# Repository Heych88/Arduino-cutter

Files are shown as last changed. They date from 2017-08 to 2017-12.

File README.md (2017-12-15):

# Arduino-cutter
Arduino controller implementation of a plastic or resistor cutter.

The controller daughter board contains the follow external board connections;

 * 6 -> 14v
 * Four push-buttons
 * Adjustable potentiometer
 * E-stops
 * 4-bit LCD
 * Single pulse encoder
 * Two solenoid relays, active low, 5v or Vin
 * Stepper motor, 2A
 * Fuse connector

## Hardware Setup

The parts required and the daughterboard PCB Gerber files are located in the EagleBoard folder.

The interfacing of the components is as follows.

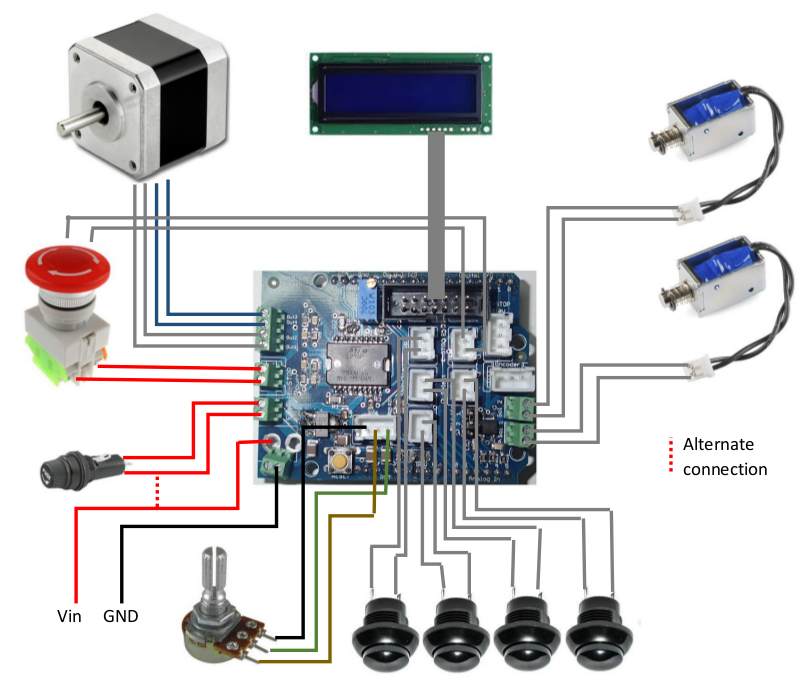
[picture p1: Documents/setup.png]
system interfacing


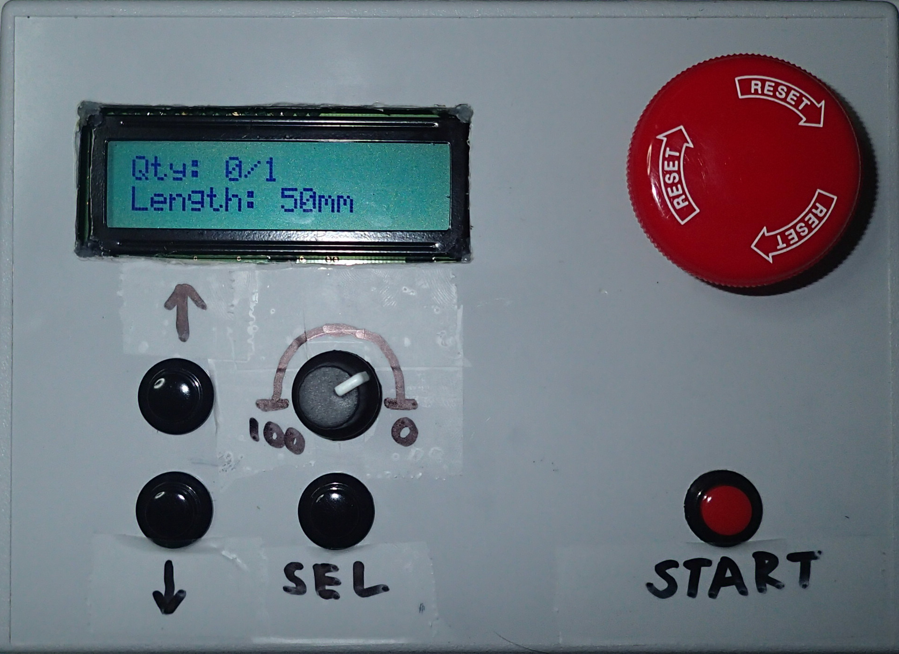
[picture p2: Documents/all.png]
assembled box


## Installing

1. Clone this repository

 ```sh
 git clone https://github.com/Heych88/Arduino-cutter.git
 ```

2. Download Arduino IDE from [here](https://www.arduino.cc/en/Main/Software).

3. If you are installing a brand-new Arduino Leonardo board, the EEPROM must be flashed first. If it is the existing system board, continue from step 4.

 1. Load the `eeprom_write.ino` file, located in the `/src/eeprom_write/` folders, into the Arduino IDE.

 2. Compile and load the file onto the Arduino board.

4. Load any of the `.ino` files, located in the `/src/` folders, into the Arduino IDE.

5. Compile and load the files onto the Arduino board.

Detailed programming and system information can be found in the *Arduino Cutter Instructions* document, located in the `/documents/` folder.

## Usage

This repository provides a daughterboard and usable code to run an Arduino plastic or resistor cutter.

## Contributing

1. Fork it!
2. Create your feature branch: `git checkout -b my-new-feature`
3. Commit your changes: `git commit -am 'Add some feature'`
4. Push to the branch: `git push origin my-new-feature`
5. Submit a pull request :D

## License

This project is licensed under the GNU-GPL3 License - see the [LICENSE.md](LICENSE.md) file for details.

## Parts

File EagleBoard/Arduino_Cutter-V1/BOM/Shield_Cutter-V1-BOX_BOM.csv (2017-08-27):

Qty | Value | MPN | Digi-key | Description
1 |  | QPC02SXGN-RC | S9337-ND | CONN JUMPER SHORTING .100" GOLD
1 |  | 61300311121 | 732-5316-ND | 3 Positions Header Connector 0.100" (2.54mm) Through Hole
1 |  | 2047 | 1528-2164-ND | POTENTIOMETER KNOB - SOFT TOUCH
1 |  | P160KN-0QC15B100K | 987-1300-ND | 100k Ohm Gang Linear Panel Mount Potentiometer None 1 Turn Conductive Plastic 0.2W, 1/5W PC Pins
1 |  | NHD-0216K1Z-FSB-GBW-L | NHD-0216K1Z-FSB-GBW-L-ND | Character LCD Display Module Transflective 5 x 8 Dots STN - Super-Twisted Nematic LED - Blue Parallel 80.00mm x 36.00mm x 13.50mm
1 |  | ROB-09238 | 1568-1105-ND | Bipolar Stepper Motor 200 Step 0.33A 12VDC
1 |  | 101-146 | ED10501-ND | 14 Position Rectangular Socket Connector IDC
1 |  | A165E-S-02 | Z1428-ND | Pushbutton Switch DPST-NC Emergency Stop Panel Mount
6 |  | XHP-2 | 455-2266-ND | 2 Position Rectangular Housing Connector Receptacle Natural 0.098" (2.50mm)
3 |  | XHP-3 | 455-2219-ND | 3 Position Rectangular Housing Connector Receptacle Natural 0.098" (2.50mm)
18 |  | SXH-001T-P0.6 | 455-1135-1-ND | Contact Crimp Socket 22-28 AWG Tin
1 |  | 1-640454-6 | A106877-ND | 16 Positions Header Connector 0.100" (2.54mm) Through Hole Tin
1 |  | 4-643814-6 | A30966-ND | 16 Position Rectangular Receptacle Connector IDC Tin 24 AWG
3 |  | RP3502ABLK | EG1900-ND | Pushbutton Switch SPST-NO Standard Panel Mount, Front, Black
1 |  | RP3502ARED | EG1930-ND | Pushbutton Switch SPST-NO Standard Panel Mount, Front, Red
1 |  | 17S,GY | SR17SG-ND | Box Plastic, ABS Gray Split Sides and Slanted Top 6.880" L x 4.880" W (174.75mm x 123.95mm) X 2.490" (63.25mm)
1 |  | A000057 | 1050-1040-ND | ATmega32U4 Arduino Leonardo AVR® ATmega MCU 8-Bit AVR Embedded Evaluation Board

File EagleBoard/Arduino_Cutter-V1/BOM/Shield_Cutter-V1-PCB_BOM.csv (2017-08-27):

Qty | Value | MPN | Digi-key | Package | Parts | Description
1 |  | 61300311121 | 732-5316-ND | JP2 | JP1 | CONN HEADER 3 POS 2.54
2 | 0R15 | RL1206FR-7W0R15L | 311-.15LYCT-ND | R1206 | R1, R2 | RES SMD 0.15 OHM 1% 1/2W 1206
1 |  | B3F-1002 | SW401-ND | B3F-10XX | RESET | SWITCH TACTILE SPST-NO 0.05A 24V
6 | 100nF | C0805C104K5RACTU | 399-1170-1-ND | C0805 | C3, C6, C7, C8, C9, C10 | 0.1µF ±10% 50V Ceramic Capacitor X7R 0805 (2012 Metric)
1 | 10k | PV36W103C01B00 | 490-2875-ND | S64W | R29 | POTENTIOMETER
12 | 10kΩ | RMCF0805FT10K0 | RMCF0805FT10K0CT-ND | R0805 | R3, R4, R10, R12, R17, R18, R19, R20, R22, R23, R25, R27 | ±1% 0.125W, 1/8W Chip Resistor 0805 (2012 Metric)
4 | 10u 35V | C1210C106K3RACTU | 399-8224-1-ND | C1210 | C1, C2, C4, C5 | CAPACITOR, European symbol
6 | 10Ω | RC0805FR-0710RL | RMCF0805FT10R0CT-ND | R0805 | R9, R11, R21, R24, R26, R28 | RES SMD 10 OHM 1% 1/8W 0805
4 | 1kΩ | RMCF0805FT1K00 | RMCF0805FT1K00CT-ND | R0805 | R5, R6, R7, R8 | ±1% 0.125W, 1/8W Chip Resistor 0805 (2012 Metric)
3 | 22-23-2021 | OSTVN02A150 | ED10561-ND | 22-23-2021 | X1, X4, X5 | .100" (2.54mm) Center Header - 2 Pin
1 | 22-23-2041 | OSTVN04A150 | ED10563-ND | 22-23-2041 | X2 | CONN TERM BLOCK 2.54MM 4POS PCB
1 | 2514- | 302-S141 | ED10522-ND | PAK100/2500-14 | X5 | 14 Positions Header Connector 0.100" (2.54mm) Through Hole
4 | 330Ω | RMCF0805FT330R | RMCF0805FT330RCT-ND | R0805 | R13, R14, R15, R16 | ±1% 0.125W, 1/8W Chip Resistor 0805 (2012 Metric)
2 | 40v | BAT54AW,115 | 1727-3567-1-ND | SOT323 | D10, D11 | Diode Array 1 Pair Common Anode Schottky 200mA (DC) Surface Mount SC-70, SOT-323
2 | AQY21SOP | CPC1020NTR | CLA318CT-ND | SOP04 | K1, K2 | PhotoMOS Relay NAiS
6 | Green | LG R971-KN-1 | 475-1410-1-ND | CHIPLED_0805 | L1, L2, L3, L4, L5, L6 | LED GREEN DIFFUSED 0805 SMD
1 | L298P | L298P | 497-1396-5-ND | POWER-SO20 | IC1 | L298P DUAL FUL-BRIDGE DRIVER PowerSO20
1 | REG1117 | REG1117-5/2K5 | 296-27924-1-ND | SOT223 | IC2 | 800mA and 1A Low Dropout (LDO) Positive Regulator
6 | S2B-PH-K | B2B-XH-A(LF)(SN) | 455-2247-ND | S02P | SV1, SV3, SV4, SV5, SV6, SV7 | CONN HEADER XH TOP 2POS 2.5MM
3 | S3B-PH-K | B3B-XH-A(LF)(SN) | 455-2248-ND | S03P | SV2, SV8, SV9 | CONN HEADER XH TOP 3POS 2.5MM
9 | SS14 | MBRAF360T3G | MBRAF360T3GOSCT-ND | SMA | D1, D2, D3, D4, D5, D6, D7, D8, D9 | DIODE SCHOTTKY 60V 4A SMA

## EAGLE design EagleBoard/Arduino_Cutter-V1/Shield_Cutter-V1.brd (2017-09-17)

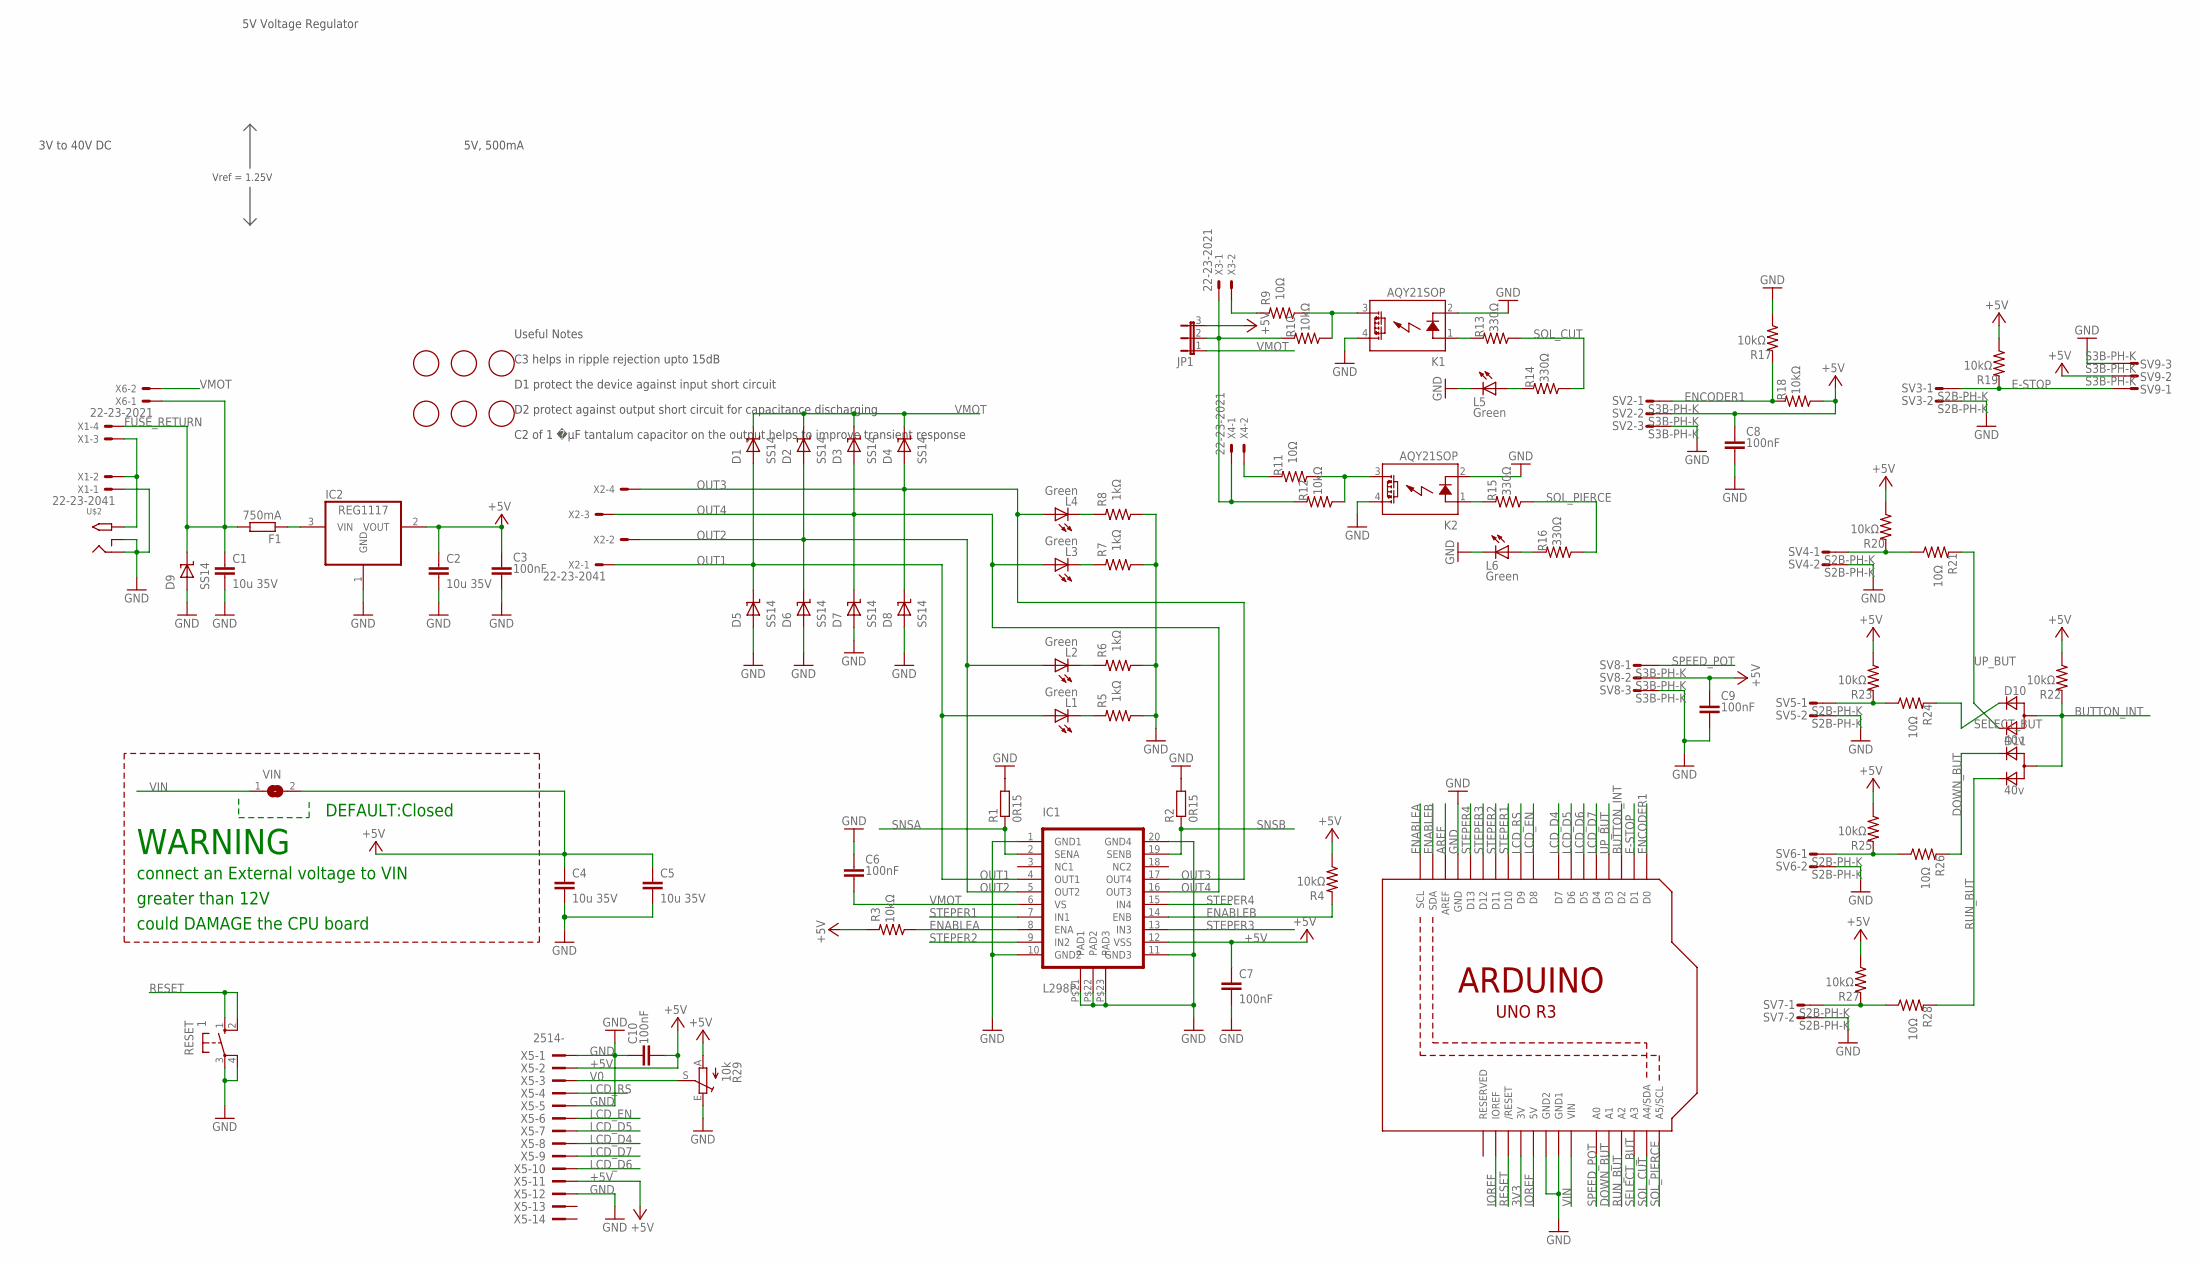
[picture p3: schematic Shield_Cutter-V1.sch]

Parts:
C1, C2, C4, C5: 10u 35V; C1210
C3, C6, C7, C8, C9, C10: 100nF; C0805
D1, D2, D3, D4, D5, D6, D7, D8, D9: SS14; SMA
D10, D11: 40v; SOT323
F1: 750mA; R1206
FID1, FID2, FID3, FID4, FID5, FID6: FIDUCIALMOUNT; FIDUCIA-MOUNT
IC1: L298P; POWER-SO20
IC2: REG1117; SOT223
JP1: JP2E; JP2
K1, K2: AQY21SOP; SOP04
L1, L2, L3, L4, L5, L6: Green; CHIPLED_0805
R1, R2: 0R15; R1206
R3, R4, R10, R12, R17, R18, R19, R20, R23, R25, R27: 10kΩ; R0805
R5, R6, R7, R8: 1kΩ; R0805
R9, R11, R21, R24, R26, R28: 10Ω; R0805
R13, R14, R15, R16: 330Ω; R0805
R22: 10kΩ; M0805
R29: 10k; S64W
RESET: 1; B3F-10XX
SV2, SV8, SV9: S3B-PH-K; S03P
SV3, SV4, SV5, SV6, SV7: S2B-PH-K; S02P
U1: ARDUINOR3-DIMENSION; ARDUINOR3
U$2: 2.1MMJACKTHM; PJ-102A
VIN: SJW
X1, X2: 22-23-2041
X3, X4, X6: 22-23-2021
X5: 2514-; PAK100/2500-14

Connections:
3V3: U1.3V
+5V: C2.1, C3.1, C4.1, C5.1, C7.1, C8.1, C9.1, C10.2, IC1.P$12 (VSS), IC2.2 (VOUT), JP1.3, R3.2, R4.1, R18.1, R19.1, R20.1, R22.1, R23.1, R25.1, R27.1, R29.A, SV2.2, SV8.2, SV9.2, VIN.2, X5.2, X5.11
AREF: U1.AREF
BUTTON_INT: D10.1 (A), D11.1 (A), R22.2, U1.D2
DOWN_BUT: D11.2 (C1), R26.2, U1.A1
E-STOP: R19.2, SV3.1, SV9.1, U1.D1
ENABLEA: IC1.P$8 (ENA), R3.1, U1.SCL
ENABLEB: IC1.P$14 (ENB), R4.2, U1.SDA
ENCODER1: R17.2, R18.2, SV2.1, U1.D0
FUSE_RETURN: C1.1, D9.P$1 (K), F1.2, X1.4, X6.1
GND: C1.2, C2.2, C3.2, C4.2, C5.2, C6.1, C7.2, C8.2, C9.2, C10.1, D5.P$2 (A), D6.P$2 (A), D7.P$2 (A), D8.P$2 (A), D9.P$2 (A), IC1.P$1 (GND1), IC1.P$10 (GND2), IC1.P$11 (GND3), IC1.P$20 (GND4), IC1.P$21 (PAD1), IC1.P$22 (PAD2), IC1.P$23 (PAD3), IC2.1 (GND), K1.2 (K), K1.4 (DS1), K2.2 (K), K2.4 (DS1), L5.C, L6.C, R1.2, R2.2, R5.1, R6.1, R7.1, R8.1, R17.1, R29.E, RESET.3, RESET.4 (P1), SV2.3, SV3.2, SV4.2, SV5.2, SV6.2, SV7.2, SV8.3, SV9.3, U1.GND, U1.GND1, U1.GND2, U$2.RING, U$2.RING_SW, X1.1, X5.1, X5.5, X5.12
IOREF: U1.5V, U1.IOREF
LCD_D4: U1.D7, X5.8
LCD_D5: U1.D6, X5.7
LCD_D6: U1.D5, X5.10
LCD_D7: U1.D4, X5.9
LCD_EN: U1.D8, X5.6
LCD_RS: U1.D9, X5.4
unnamed: L4.C, R8.2
unnamed: L3.C, R7.2
unnamed: L2.C, R6.2
unnamed: L1.C, R5.2
unnamed: K1.1 (A), R13.2
unnamed: L5.A, R14.2
unnamed: R9.2, X3.2
unnamed: R23.2, R24.1, SV5.1
unnamed: JP1.2, R10.2, R12.2, X3.1, X4.1
unnamed: K2.3 (DS2), R11.1, R12.1
unnamed: L6.A, R16.2
unnamed: R20.2, R21.1, SV4.1
unnamed: K2.1 (A), R15.2
unnamed: R11.2, X4.2
unnamed: K1.3 (DS2), R9.1, R10.1
unnamed: R25.2, R26.1, SV6.1
unnamed: F1.1, IC2.3 (VIN)
unnamed: R27.2, R28.1, SV7.1
OUT1: D1.P$2 (A), D5.P$1 (K), IC1.P$4 (OUT1), L1.A, X2.1
OUT2: D2.P$2 (A), D6.P$1 (K), IC1.P$5 (OUT2), L2.A, X2.2
OUT3: D4.P$2 (A), D8.P$1 (K), IC1.P$17 (OUT4), L4.A, X2.4
OUT4: D3.P$2 (A), D7.P$1 (K), IC1.P$16 (OUT3), L3.A, X2.3
POWERIN: U$2.TIP, X1.2, X1.3
RESET: RESET.1 (S), RESET.2 (S1), U1.RESET (/RESET)
RUN_BUT: D11.3 (C2), R28.2, U1.A2
SELECT_BUT: D10.2 (C1), R24.2, U1.A3
SNSA: IC1.P$2 (SENA), R1.1
SNSB: IC1.P$19 (SENB), R2.1
SOL_CUT: R13.1, R14.1, U1.A4 (A4/SDA)
SOL_PIERCE: R15.1, R16.1, U1.A5 (A5/SCL)
SPEED_POT: SV8.1, U1.A0
STEPER1: IC1.P$7 (IN1), U1.D10
STEPER2: IC1.P$9 (IN2), U1.D11
STEPER3: IC1.P$13 (IN3), U1.D12
STEPER4: IC1.P$15 (IN4), U1.D13
UP_BUT: D10.3 (C2), R21.2, U1.D3
V0: R29.S, X5.3
VIN: U1.VIN, VIN.1
VMOT: C6.2, D1.P$1 (K), D2.P$1 (K), D3.P$1 (K), D4.P$1 (K), IC1.P$6 (VS), JP1.1, X6.2

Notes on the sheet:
WARNING
connect an External voltage to VIN
greater than 12V
could DAMAGE the CPU board
DEFAULT:Closed
5V Voltage Regulator
C3 helps in ripple rejection upto 15dB
D1 protect the device against input short circuit
D2 protect against output short circuit for capacitance discharging
C2 of 1 �µF tantalum capacitor on the output helps to improve transient response
Useful Notes
5V, 500mA
3V to 40V DC
Vref = 1.25V

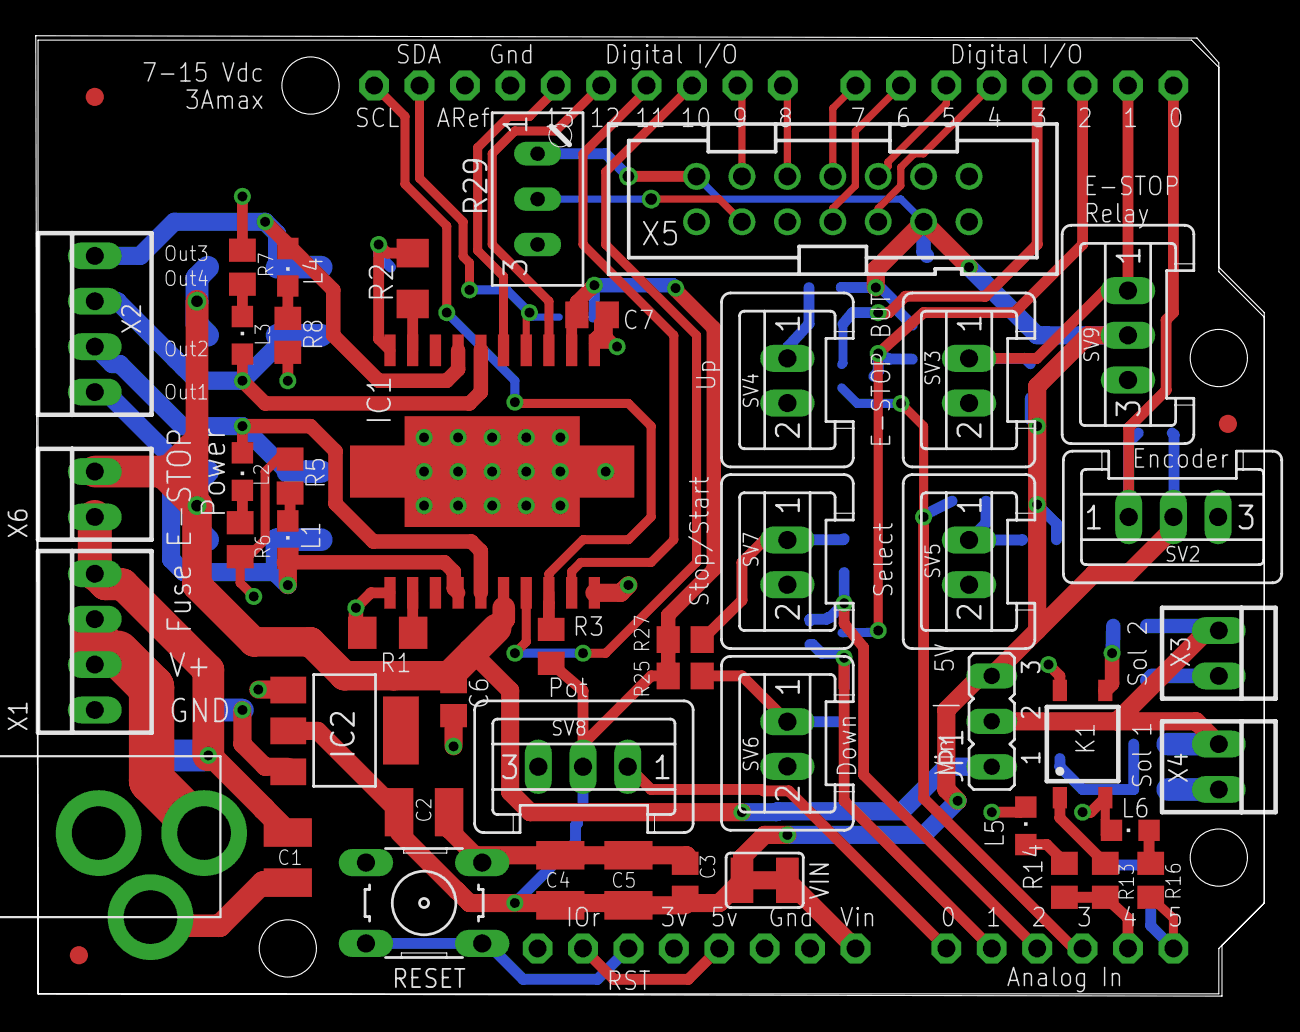
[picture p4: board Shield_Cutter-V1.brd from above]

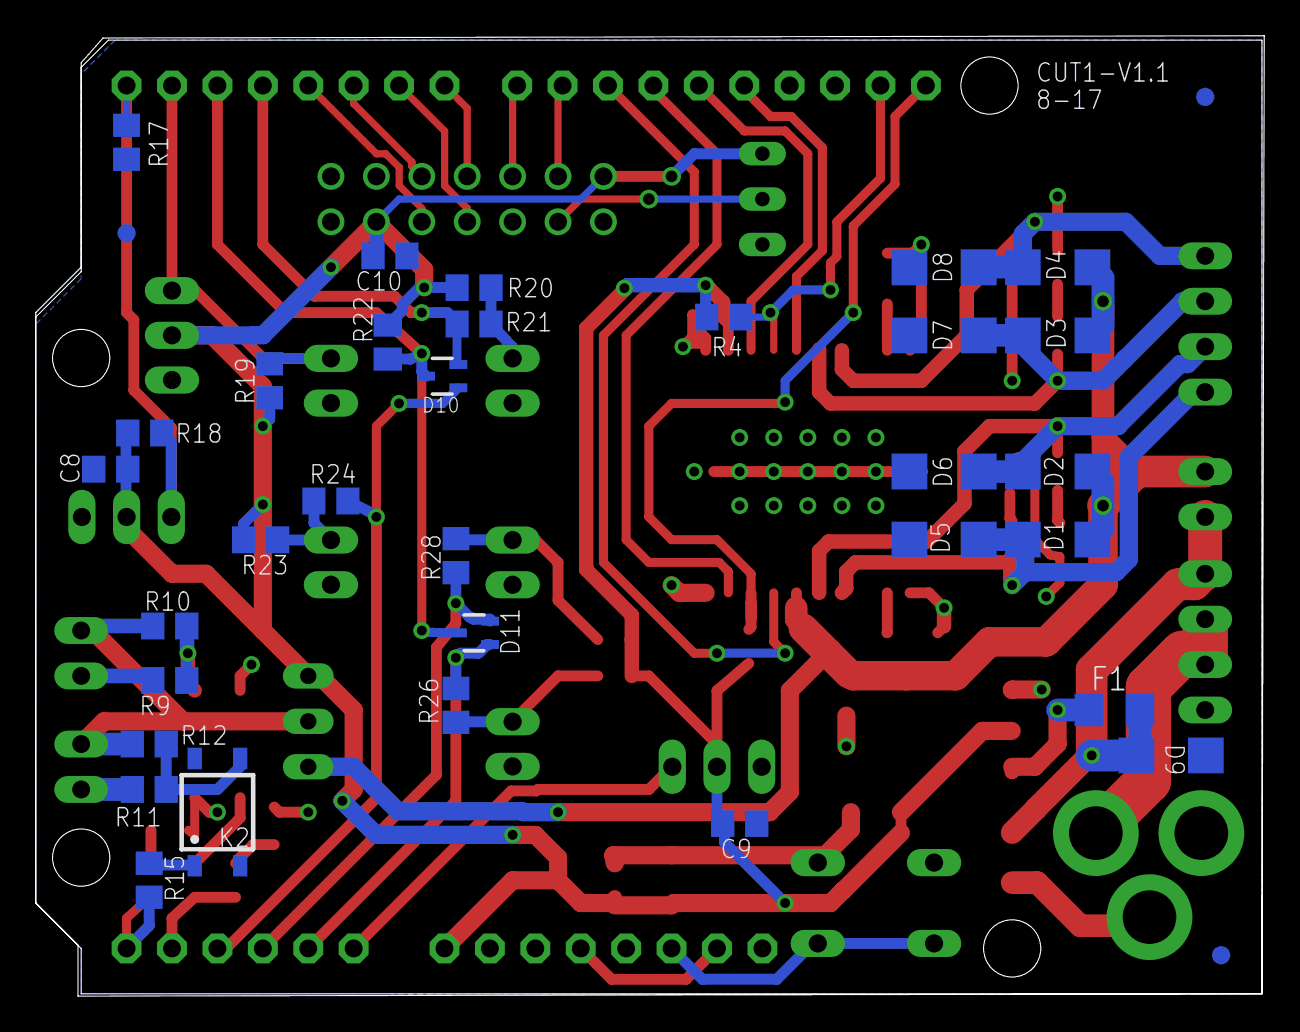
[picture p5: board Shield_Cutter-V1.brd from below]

Board: 2 copper layers, 68.7 x 53.7 mm, 86 parts (35 on the bottom side), 55 nets.

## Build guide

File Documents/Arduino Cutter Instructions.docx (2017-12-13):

# Setup

## Specifications

Power supply: 6 -> 14vdc, center positive

Fuse: 3A Max, 5x20mm glass fuse

Solenoid: 5v or Vin

Stepper motor: Vin, 5mm shaft, bipolar

## Hardware Setup

The system contains the follow external board connections;

- Five push-buttons
- Adjustable potentiometer
- Two E-stops, one active, one passive.
- 4-bit LCD
- Single pulse encoder
- Two solenoid relays, active low
- Stepper motor driver
- Fuse connector
- Power

The hardware parts list, PCB files and program, can be downloaded from the Git repository;

https://github.com/Heych88/Arduino-cutter

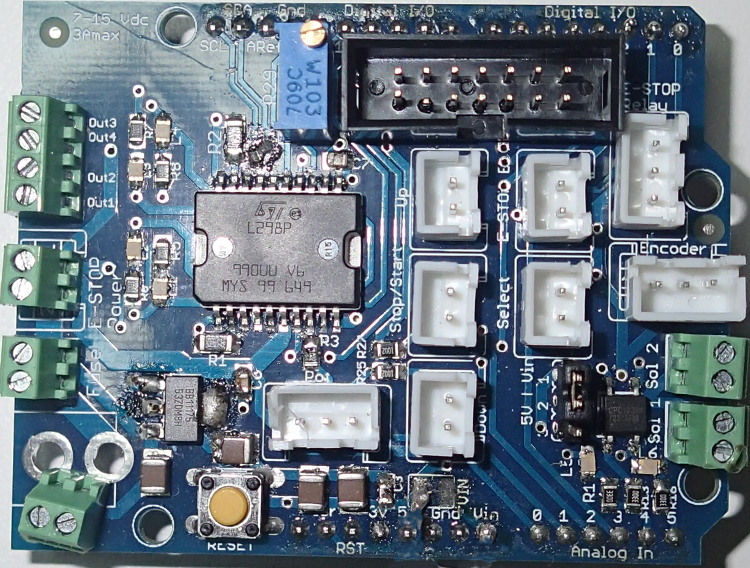
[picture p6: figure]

Stepper motor

E-stop return

E-stop Vin

Fuse return

Fuse Vin

Vin

Solenoid outputs

4-bit LCD

Solenoid voltage select

GND

Reset

E-stop sense

Up PB

E-stop active S + -

S

Select PB

Stop/Start PB

S

S

Encoder S + -

Pot - + S

Down PB

The wiring of the hardware, for most common operations, is as follows;

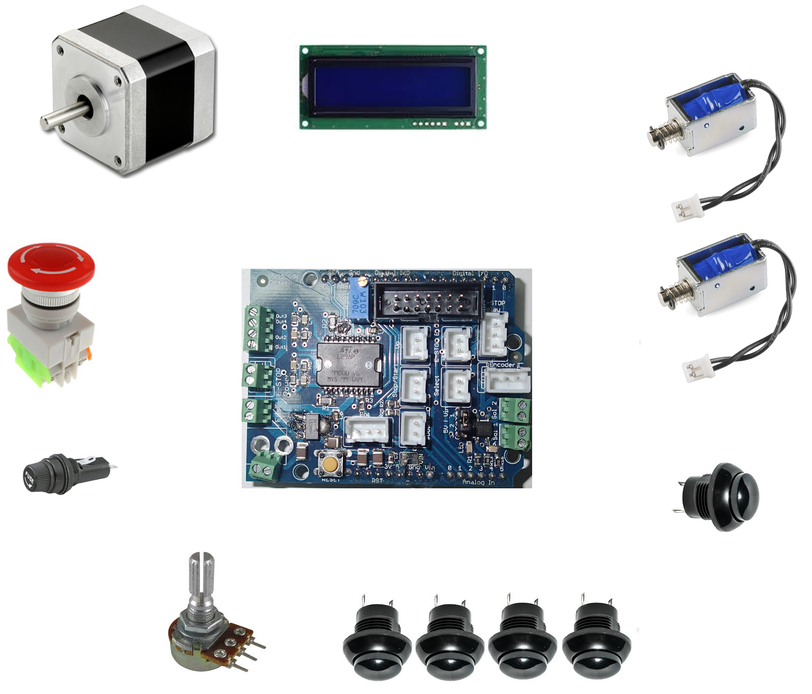
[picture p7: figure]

Alternate connection

Pierce

Cut

Up Down Stop/Stat Select

Vin GND

### Motor rotation direction

Upon installation of a stepper motor, the two winding pairs must be located. It is recommended to use a multimeter to measure the resistance between the wires. One winding pair must then be connected into the output connector group pairing of Out1 and Out2 and the second winding pair connected to Out3 and Out4.

Once connected, the motor will spin in a direction. If the motor is required to spin in the reverse direction, swap the group pairings with each other. I.e. Out1 swap with Out3, Out2 swap with Out4.

### Solenoid power selection

The solenoids can be supplied with either 5v or Vin. Both solenoids must power from the same supply and must both be either 5v or Vin.

The voltage can be changed by swapping the jumper on header JP1. See board for voltage configuration details.

For 5v solenoids, place the jumper on pins 1 and 2. For Vin solenoids, put the jumper on pins 2 and 3.

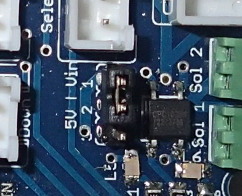
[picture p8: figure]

## Software Setup

### Menu Selection

The controller contains 11 adjustable menu selections. Six for adjusting production runs and five for system specific hardware setup.

To enter the system menu, press the up button.

To navigate the system menu, press either the up or down buttons.

To select a menu, press the SEL button, and a flashing cursor will appear on the screen.

### Production Run Settings

#### Adjust quantity

Adjusts the desired production quantity to be produced with the desired product specifications, as outlined in other sections.

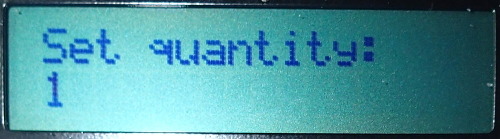
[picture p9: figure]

1. Navigate to the "Set quantity" menu using the UP or DOWN buttons.
2. Press the SEL button, and a flashing cursor will appear. If the flashing cursor doesn’t appear, press the SEL button until it does.
3. Adjust the desired quantity using the UP or DOWN buttons.
4. Press the SEL button to set the desired quantity and return to the home screen.

#### Adjust length

Adjusts the total desired product length.

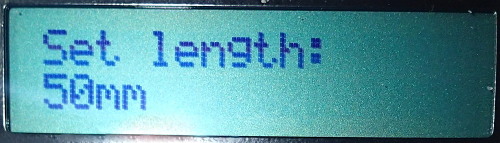
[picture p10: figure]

1. Navigate to the "Set length" menu using the UP or DOWN buttons.
2. Press the SEL button, and a flashing cursor will appear. If the flashing cursor doesn’t appear, press the SEL button until it does.
3. Adjust the desired length using the UP or DOWN buttons.
4. Press the SEL button to set the desired length and return to the home screen.

#### Reset production counts

Resets the number of the already produced product.

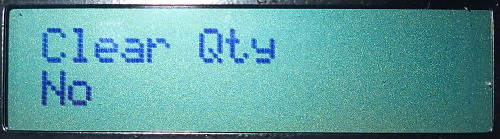
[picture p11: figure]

1. Navigate to the "Clear Qty" menu using the UP or DOWN buttons.
2. Press the SEL button, and a flashing cursor will appear. If the flashing cursor doesn’t appear, press the SEL button until it does.
3. Press the UP button until the display changes to "Yes".
4. Press the SEL button to rest the produced quantity and return to the home screen.

#### Adjust motor speed menu

Adjusts the motors running speed. This menu is only used for display purposes only.

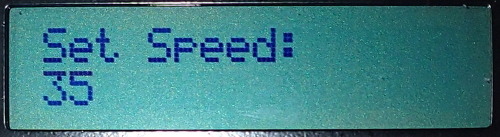
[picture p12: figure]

1. Navigate to the "Set Speed" menu using the UP or DOWN buttons.
2. Adjust the speed using the SPEED DIAL until at the desired speed.
3. Navigate to the home menu with the DOWN button.

#### Adjust pierce distance

Adjusts the distance from the end of the desired length to add a pierce.

If the number of pierces is two, a pierce is performed at the desired distance from the start of piece and the desired distance from the final length of the part.

If the number of pierces is one, a pierce is only performed at the desired distance from the start of piece.

The pierce distance is calculated from the product edges and the centre of the piercing die.

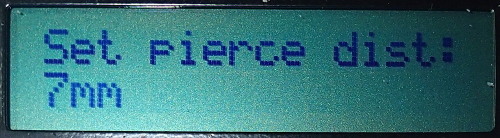
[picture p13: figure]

1. Navigate to the "Set pierce dist" menu using the UP or DOWN buttons.
2. Press the SEL button, and a flashing cursor will appear. If the flashing cursor doesn’t appear, press the SEL button until it does.
3. Adjust the desired length using the UP or DOWN buttons.
4. Press the SEL button to set the desired distance and return to the home screen.

#### Adjust pierce quantity

Resets the number of piercings in each product piece.

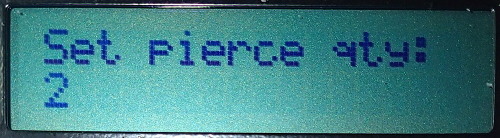
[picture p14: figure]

1. Navigate to the "Set pierce qty" menu using the UP or DOWN buttons.
2. Press the SEL button, and a flashing cursor will appear. If the flashing cursor doesn’t appear, press the SEL button until it does.
3. Adjust the desired quantity using the UP or DOWN buttons.
4. Press the SEL button to set the quantity and return to the home screen.

### Hardware Setup

#### Adjust pierce solenoid delay

Adjusts the time delay for activating and deactivating the solenoid used for piercing in milliseconds.

The total solenoid time is double the delay time set, as the delay time set is the full time that the solenoid is activated (set Low) and the identical time to release and retract the solenoid (set High) back to its deactivated state.

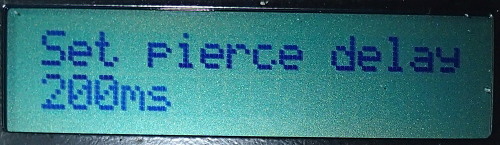
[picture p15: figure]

1. Navigate to the "Set pierce delay" menu using the UP or DOWN buttons.
2. Press the SEL button, and a flashing cursor will appear. If the flashing cursor doesn’t appear, press the SEL button until it does.
3. Adjust the desired delay using the UP or DOWN buttons.
4. Press the SEL button to set the required delay time and return to the home screen.

#### Adjust cut solenoid delay

Adjusts the time delay for activating and deactivating the solenoid used for cutting in milliseconds.

The total solenoid time is double the delay time set, as the delay time set is the entire time that the solenoid is activated (set Low) and the identical time to release and retract the solenoid (set High) back to its deactivated state.

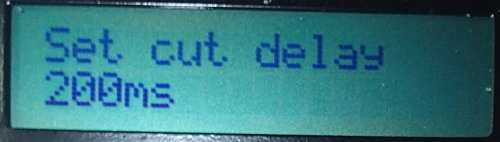
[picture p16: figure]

1. Navigate to the "Set cut delay" menu using the UP or DOWN buttons.
2. Press the SEL button, and a flashing cursor will appear. If the flashing cursor doesn’t appear, press the SEL button until it does.
3. Adjust the desired delay using the UP or DOWN buttons.
4. Press the SEL button to set the required delay time and return to the home screen.

#### Adjust stepper motor counts per rotation

Changes the number of steps for one full stepper motor revolution.

This is specific to each motor. Check the datasheet of the motor for more information.

If a geared system is used, the gear ratio must be factored into consideration here. I.e. a motor step count of 200 with a motor to wheel gear ration of 10:1, set the step count to 2000.

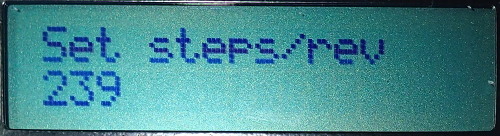
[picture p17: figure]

1. Navigate to the "Set steps/rev" menu using the UP or DOWN buttons.
2. Press the SEL button, and a flashing cursor will appear. If the flashing cursor doesn’t appear, press the SEL button until it does.
3. Adjust the steps using the UP or DOWN buttons.
4. Press the SEL button to set the required steps and return to the home screen.

#### Adjust drive wheel diameter

Adjusts the diameter of the drive wheel that is driven by the drive motor.

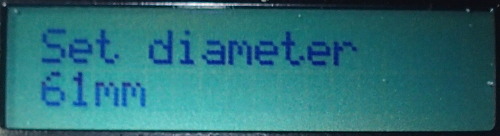
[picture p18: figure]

1. Navigate to the "Set diameter" menu using the UP or DOWN buttons.
2. Press the SEL button, and a flashing cursor will appear. If the flashing cursor doesn’t appear, press the SEL button until it does.
3. Adjust the diameter using the UP or DOWN buttons.
4. Press the SEL button to set the diameter and return to the home screen.

#### Adjust solenoid offset

Adjusts the distance between the pierce and cut solenoids in mm.

The pierce solenoid is MUST be placed before the cutting solenoid, in the direction of travel.

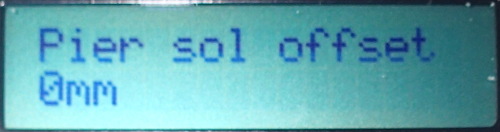
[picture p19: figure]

1. Navigate to the "Pier sol offset" menu using the UP or DOWN buttons.
2. Press the SEL button, and a flashing cursor will appear. If the flashing cursor doesn’t appear, press the SEL button until it does.
3. Adjust the offset distance between the cutting blade and the centre of the piercing die using the UP or DOWN buttons.
4. Press the SEL button to set the required steps and return to the home screen.

# Programming with Arduino IDE

The brains behind the program is an Arduino Leonard.

A new Leonardo can be programmed using the Arduino IDE which can be downloaded for free from the Arduino site;

https://www.arduino.cc/en/Main/Software

Install the software as required by your operating system. I.e. For windows download and run the .exe file.

## Programming the EEPROM

If you are installing a brand-new Arduino Leonardo board, the EEPROM must be flashed first. If it is the existing system board, this step can be skipped.

The code can be downloaded from the Git repository;

https://github.com/Heych88/Arduino-cutter

1. Run the Arduino IDE
2. Click File > Open

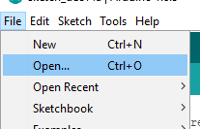
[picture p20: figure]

3. Navigate to the programs code location and select the eeprom_write.ino file by navigating to <Saved path>/src/eeprom_write/eeprom_write.ino

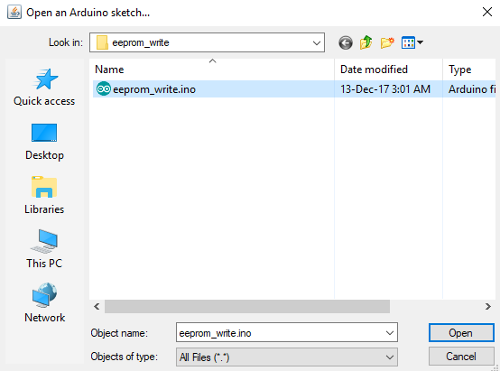
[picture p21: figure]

4. Click open
5. Set the board type under Tools > Board, select Arduino Leonardo.

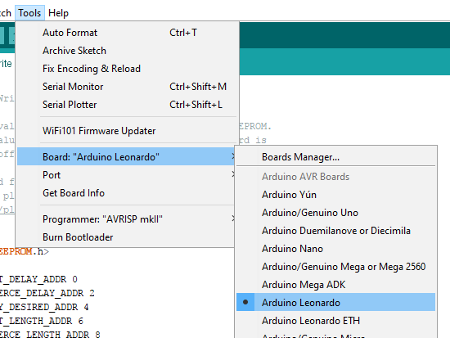
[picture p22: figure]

6. Connect the Arduino board to the computer using the micro USB port. It is recommended to remove all other external power supplies before and during USB connection to the PC.
7. Assign the correct computer port that the Arduino is connected too, under Tools > Port > COMx (Arduino Leonard).

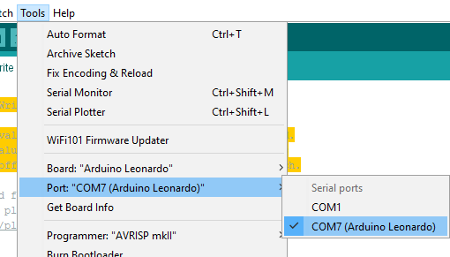
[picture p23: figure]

Note: The COM port used above may vary between machines.

8. On the main screen, click the Verify icon, tick icon. This will compile the program.
9. If no errors have occurred, click on the Upload icon, arrow icon.
10. Once uploaded the program will run automatically, and when complete, the program will turn on Pin 13 LED.
11. If Pin13 LED, onboard LED ‘L ‘, is on. You have successfully loaded the EEPROM onto the device. You can now move onto the main program load sequence.

## Programming the system program

If you are installing a brand-new Arduino Leonardo board, the EEPROM must be flashed first. See above for details.

The code can be downloaded from the Git repository;

https://github.com/Heych88/Arduino-cutter

1. Run the Arduino IDE
2. Click File > Open
3. Navigate to the programs code location and select any .ino file by navigating to <Saved path>/src/xxx.ino

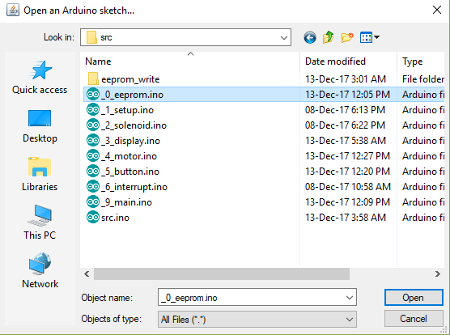
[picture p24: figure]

4. Click open
5. Set the board type under Tools > Board, select Arduino Leonardo.
6. Connect the Arduino board to the computer using the micro USB port. It is recommended to remove all other external power supplies before and during USB connection to the PC.
7. Assign the correct computer port that the Arduino is connected too, under Tools > Port > COMx (Arduino Leonard).

Note: The COM port used above may vary between machines.

8. On the main screen, click the Verify icon, tick icon. This will compile the program.
9. If no errors have occurred, click on the Upload icon, arrow icon.
10. Once uploaded, the board can be unplugged from the PC, and the system power can be plugged in again. Upon powerup, the system will operate as usual.

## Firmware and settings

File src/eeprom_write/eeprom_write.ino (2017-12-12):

/*
 * EEPROM Write
 *
 * Stores values read from analog input 0 into the EEPROM.
 * These values will stay in the EEPROM when the board is
 * turned off and may be retrieved later by another sketch.
 * 
 * Modified from the Arduino example eeprom_write.ino and 
 * arduino playground
 * https://playground.arduino.cc/Code/EEPROMReadWriteLong
 */

#include <EEPROM.h>

#define CUT_DELAY_ADDR 0
#define PIERCE_DELAY_ADDR 2
#define QTY_DESIRED_ADDR 4
#define CUT_LENGTH_ADDR 6
#define PIERCE_LENGTH_ADDR 8
#define PIERCE_QTY_ADDR 10
#define WHEEL_DIAM_ADDR 12
#define STEP_REV_ADDR 14
#define SOL_OFFSET_ADDR 16


int addr = 0;
int int_size = sizeof(int);

const int cut_delay = 200;  // delay between solenoid cutting and activation
const int pierce_delay = 200;

const int qty_desired = 1; // total number of sleeves required for production
const int cut_length = 50; // length of each piece
const int pierce_length = 7; // length of each piece
const int qty_pierce = 3; // length of each piece

const int wheel_diam = 61.0;  // diameter of the wheel
const int steps_per_revolution = 239;  // change this to fit the number of steps per revolution for your motor
const int pierce_sol_offset = 0;  // Offset between the cutting solenoid and the pierce solenoid.
                            // Pierce solenoid my be placed before the cut solenoid in the direction of travel.

/*
 * Splits int (16bit) values into bytes and stores them into 8bit EEPROM starting at the desired address.
 * 
 * Args:
 *    address: EEPROM address to store the values
 *    value: integer value to store at the address
 */
void eepromWrite(int address, int value)
{
  //Decomposition from a long to 4 bytes by using bitshift.
  //One = Most significant -> Four = Least significant byte
  byte one = (value & 0xFF);
  byte two = ((value >> 8) & 0xFF);

  //Write the 4 bytes into the eeprom memory.
  EEPROM.write(address, one);
  EEPROM.write(address + 1, two);
}


void setup() {
  // initialize the LED pin as an output.
  pinMode(13, OUTPUT);

  // Clear the EEPROM
  for (int i = 0 ; i < EEPROM.length() ; i++) {
    EEPROM.write(i, 0);
  }
  
  eepromWrite(CUT_DELAY_ADDR, cut_delay);
  eepromWrite(PIERCE_DELAY_ADDR, pierce_delay);
  eepromWrite(QTY_DESIRED_ADDR, qty_desired);
  eepromWrite(CUT_LENGTH_ADDR, cut_length);
  eepromWrite(PIERCE_LENGTH_ADDR, pierce_length);
  eepromWrite(PIERCE_QTY_ADDR, qty_pierce);
  eepromWrite(WHEEL_DIAM_ADDR, wheel_diam);
  eepromWrite(STEP_REV_ADDR, steps_per_revolution);
  eepromWrite(SOL_OFFSET_ADDR, pierce_sol_offset);

  // turn the LED on when we're done
  digitalWrite(13, HIGH);
}

void loop() {
  
}

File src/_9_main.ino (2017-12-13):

/*
 * Function to produce one sleeve with the desired sleeve settings. 
 * 
 * Args:
 *    None
 *    
 */
void runOneSleeve(){
  
  if(qty_pierce > 0) {
    motor_run(getDistanceCount(pierce_length - pierce_sol_offset) + 1);
    pierce_solenoid();
  
    if(qty_pierce == 2){
      motor_run(getDistanceCount(cut_length - (2 * pierce_length)));
      pierce_solenoid();
      motor_run(getDistanceCount(pierce_length + pierce_sol_offset) + 1);
    } else {
      motor_run(getDistanceCount(cut_length - pierce_length + pierce_sol_offset));
    }
  }else{
    motor_run(getDistanceCount(cut_length));
  }

  cut_solenoid(); // cut sleeve to desired length

  qty_current += 1;
}

/* 
 * main program loop 
 * 
 */
void loop() {
  
  if (e_stop_active) {
    start_active = false;
    // E-Stop is active so stop the machine
    eStop();
    state = MAIN;
    
    delay(1000);
    
  } else {
    // check if the start button is active to run the system
    if (start_active) {
      state = MAIN;
            
      while((qty_current < qty_desired) && (e_stop_active == false) && (start_active)) {
        // Normal running program
        pollButton();

        getSpeed(); // update the desired_speed
        if(desired_speed > 1) {
          runOneSleeve();
        } else {
          start_active = false;
        }

        homeMenu(); // update the display to show the current qty
        delay(100);
      }
      start_active = false;
    } 
    
    motor_stop();
    pollButton();

    if ((!menu_selected) && (state == MAIN)) homeMenu();
    if (!e_stop_active) delay(100);
  }
}

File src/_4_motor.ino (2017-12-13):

/*
 * Calculates the travel distance of the wheel per step of the stepper 
 * 
 * Args:
 *    distance: The required distance for the wheel to travel        
 *    
 * Returns:
 *    The step counts required to travel the distance
 */
int getDistanceCount(const int distance){
  
  float wheel_dist_per_step = (wheel_diam * PI) / stepsPerRevolution; // distance travelled per step
  return int((distance / wheel_dist_per_step) + 0.5);
}


/*
 * Stops the stepper motor and deactivates it to prevent current draw during non use.
 * 
 * Args:
 *    None
 *    
 */
void motor_stop() {
  start_active = false;
  digitalWrite(SDA, LOW);
}


/*
 * Initalises and runs the stepper motor to the desired distance.
 * 
 * Args:
 *    steps: number of steps to mover the motor.
 *    
 */
void motor_run(const int steps) {
  // check that the pwm value is within the desired threshholds
  if ((e_stop_active) || (start_active == false) || (desired_speed <= 1)) {
    motor_stop();
  } else {
    auto myStepper = new Stepper(stepsPerRevolution, 10, 11, 12, 13);
    
    digitalWrite(SDA, HIGH); // Enable the motor driver

    myStepper->setSpeed(desired_speed+2);
    myStepper->step(steps);
    digitalWrite(SDA, LOW);

    delete myStepper;
  }  
}

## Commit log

2017-07-28 add motor control
2017-07-31 Feat: add stop/start button and E-Stop polling
2017-08-02 Feat: add cut length menu and adjustment
2017-08-05 Feat: add pcb board
    [Shield_Cutter-V1.brd, Shield_Cutter-V1.sch]
2017-08-06 Feat: pcb routed
    [Shield_Cutter-V1.brd, Shield_Cutter-V1.sch]
2017-08-06 Feat: add pcb ground plane
    [Shield_Cutter-V1.brd]
2017-08-06 Feat: add text on silk screen
    [Shield_Cutter-V1.brd]
2017-08-06 Feat: init gerber files
    [Shield_Cutter-V1.GBL, Shield_Cutter-V1.GBO, Shield_Cutter-V1.GBS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]
2017-08-07 FIX: increase components to 0805 size
    [Shield_Cutter-V1.brd, Shield_Cutter-V1.sch]
2017-08-07 Chore: gerbers and files for pcb manufacture
    [Shield_Cutter-V1.brd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]
2017-08-08 Chore: add part names to pcb and cap from vmot to ground
    [Shield_Cutter-V1.brd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]
2017-08-08 chore: init BOM's
    [Shield_Cutter-V1-BOX_BOM.csv, Shield_Cutter-V1-PCB_BOM.csv]
2017-08-27 chore: update BOM
    [Shield_Cutter-V1-BOX_BOM.csv, Shield_Cutter-V1-PCB_BOM.csv]
2017-09-12 Fix: fix floating ground. Feat: add power input terminal.
    [Shield_Cutter-V1.brd, Shield_Cutter-V1.sch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]
2017-09-17 Feat: add fuse to 5v power
    [Shield_Cutter-V1.brd, Shield_Cutter-V1.sch]
2017-09-21 chore: update E-STOP to new board
2017-09-21 chore: update push-buttons to new board
2017-09-21 feat: add stepper motor to new board
2017-10-23 Fix: stepper motor stop and overheat
    [_0_setup.ino, _9_main.ino]
2017-10-26 Feat: push button interrupt enabled
2017-10-30 Fix: motor overheat minimise
    [_9_main.ino]
2017-10-30 Feat: add solenoid
2017-11-06 Feat: add button features
2017-11-06 Feat: add solenoids
2017-11-13 Feat: clear current qty
2017-11-14 Feat: adjustable solenoid delay
2017-11-15 fix: speed at zero stops all
    [_9_main.ino]
2017-11-15 Fix: motor run after speed is zero
    [_9_main.ino]
2017-11-15 Fix: qty count on speed stop
    [_9_main.ino]
2017-11-16 fix: distance steps change: move motor prams to motor file
2017-12-07 Fix: steps for each length maths
    [_0_setup.ino, _9_main.ino]
2017-12-07 Feat: add adjustable steps per stepper motor revolution
2017-12-08 Feat: add adjustable drive wheel diameter
2017-12-08 Change: move stepper class into drive loop
2017-12-12 Feat: Remove serial to prevent lockup
    [eeprom_write.ino]
2017-12-13 Feat: add pierce solenoid offset from cut solenoid
